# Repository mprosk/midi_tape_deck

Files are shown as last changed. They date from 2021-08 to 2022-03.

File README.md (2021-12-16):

# MIDI Tape Deck
MIDI controlled tape deck. Dynamically adjust the pitch of a recording to a specific pitch based on MIDI note data.

This project is built around the Yamaha KX-130 but can likely be adapted to other decks and mechanisms

## Theory of Operation

Cassette tapes are designed to run at a nominal rate of 1.75 inches per second. When the speed of tape playback is changed, the resulting sound will have a change in pitch. The slower the speed, the lower the pitch, and vice versa. By adjusting the speed of tape playback by a specific amount, the pitch of the recording can be changed to a specific note, assuming the nominal pitch of the recording is known.

This project provides the hardware and software for performing such a task.

### Speed Control

In the tape deck used in this project, the tape speed could be adjusted using a 1k potentiometer. The pitch range of the 1k pot was quite limited, meaning that few notes could be reached. Experimentation revealed that the larger the value of the potentiometer, the larger the change in frequency, and thus the more notes that could be tuned to. In addition, the change in pitch as a function of the change of resistance was observed to be linear.

Digital potentiometers are one way of interfacing digital and analog systems. The value of the pot can be changed in software but wired to the tape deck in place of the existing 1k pot. However, digital potentiometers typically have only 128 or 256 "taps" on them, meaning they can only stop at a fairly low number of values between the minimum and maximum values. This is in contrast to the mechanically actuated potentiometer, which can be adjusted continuously along is range.

Due to the low number of taps, a single digital potentiometer would not be able to control the tape deck with enough precision to reach a specific note. In order to mitigate this, two digital potentiometers were ganged together in the circuit shown below.

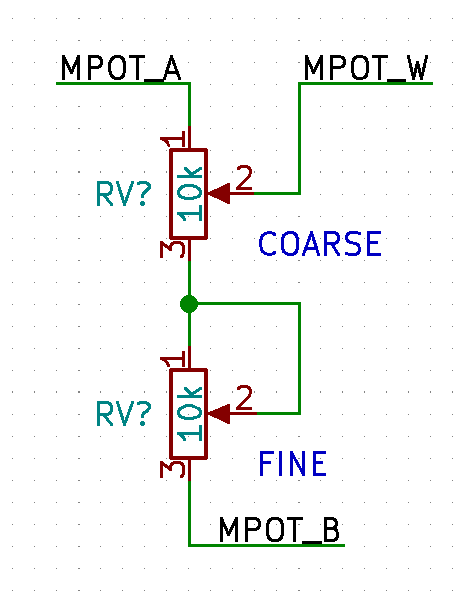
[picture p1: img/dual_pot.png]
dual_pot


This configuration results in one of the potentiometers causing a larger change in the overall resistance, while the other produced a larger change, creating a "coarse" setting and a "fine" setting. This configuration allowed for a much larger number of frequencies to be reached, as  instead of 256 discrete points, there were now 256<sup>2</sup> different combinations across the two potentiometers. 

### Transfer Function

The purpose of the potentiometers is to adjust the playback speed of the tape such that the frequency is changed by a target amount. In order to know what values to set the potentiometers to, we must know what the relationship between the potentiometer settings and the change in frequency is in the first place. By understanding this relationship, we can figure out what pot settings we need to obtain the desired change in pitch.

This system has two independent variables--the settings of the coarse and fine potentiometers--and one dependent variable--the change in pitch of the tape. By stepping through a range of combinations of potentiometers settings and recording the resulting pitch shift, we can start to see the relationship develop.

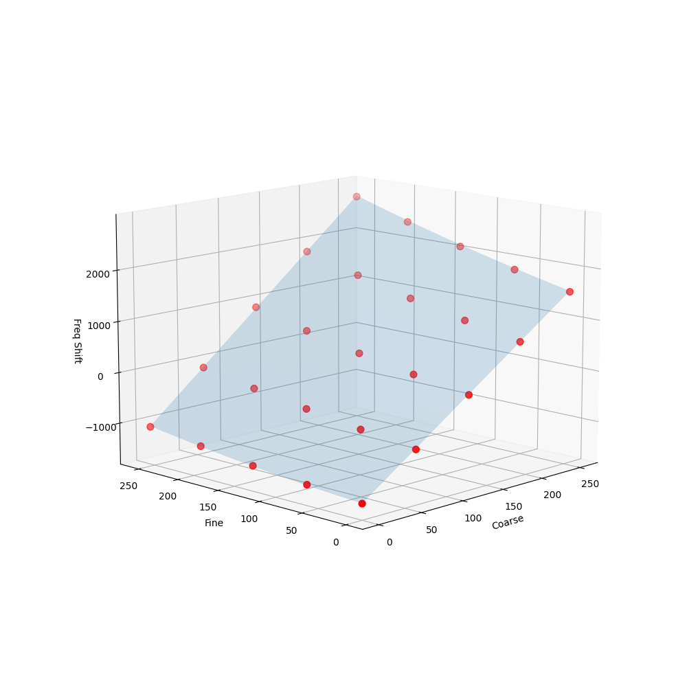
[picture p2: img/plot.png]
plot


Note that this relationship is only linear when the coarse potentiometer is changed, and is nonlinear when the fine potentiometer is changed. Also note how the coarse potentiometer has a greater impact on the output frequency than the fine potentiometer. 

Once we have captured enough data points, a best fit equation can be calculated for the surface using polynomial regression. This is performed in `eval/eval.py`. This produces a formula that equates the change in output frequency based on the coarse (x) and fine (y) potentiometer settings.

```
freq(x,y) = -1503.0871471 + 12.0767089x + 0.9015391y + 0.0115233xy + 0.003259y^2
```

### Equation Solver

Now that we are able to calculated the change in output frequency for a given combination of coarse and fine settings, we can start to work on the inverse: finding the combination of potentiometer settings that result in the desired change in output frequency.

Solving the equation mathematically for a given frequency is not conducive to an embedded device (or me) so this approach will be a little more brute-force, essentially a recursive guess-and-check.

First, the setting of the fine potentiometer is fixed to 127. A binary search is performed on the setting of the coarse potentiometer, using the equation above to determine what the output frequency will be. Once a coarse settings is found that puts the output close enough to the target value, the same operation is repeated for the fine potentiometer. Essentially the coarse pot is adjust to get the output close, then final adjustment is made using the fine pot.

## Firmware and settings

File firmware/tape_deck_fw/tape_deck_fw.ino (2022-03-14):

/***********************************************************************
 *  MIDI Tape Deck
 *
 *  DESCRIPTION
 *      <TODO>
 *
 *  REFERENCES
 *      
 * 
 ***********************************************************************/

/*=====================================================================*
    Local Header Files
 *=====================================================================*/


/*=====================================================================*
    Interface Header Files
 *=====================================================================*/
#include "mcp41hvx1.h"
#include "midi.h"
#include "notes.h"


/*=====================================================================*
    System-wide Header Files
 *=====================================================================*/
#include <Arduino.h>
#include <math.h>


/*=====================================================================*
    Pin Defines
 *=====================================================================*/
#define PIN_MODE_SW                 (2)
#define PIN_INT_1                   (3)
#define PIN_POT_COARSE              (A4)
#define PIN_POT_FINE                (A5)
#define PIN_LED                     (A0)


/*=====================================================================*
    Private Defines
 *=====================================================================*/
// #define DEBUG_PRINTOUT              /* Enables debug printing */
#define LED_BLINK_INTERVAL_MS       (1000u)

/*=====================================================================*
    Private Data Types
 *=====================================================================*/
/* None */


/*=====================================================================*
    Private Data
 *=====================================================================*/



/*=====================================================================*
    Ardunio Function Implementations
 *=====================================================================*/

void setup()
{

    // Initialize UART for MIDI
      Serial.begin(31250);      // This is the CORRECT MIDI baud rate
//    Serial.begin(32190);        // This is to compensate for the Virus's overzealous clock rate

    // Initialize GPIO
    pinMode(PIN_MODE_SW, INPUT_PULLUP);
    pinMode(PIN_LED, OUTPUT);
    digitalWrite(PIN_LED, LOW);
    

    // Initialize MCP41HVx1
    pinMode(PIN_POT_COARSE, OUTPUT);
    pinMode(PIN_POT_FINE, OUTPUT);
    digitalWrite(PIN_POT_COARSE, HIGH);
    digitalWrite(PIN_POT_FINE, HIGH);
    SPI.begin();
    SPI.beginTransaction(SPISettings(MCP41HVX1_SPI_CLK_HZ, MSBFIRST, SPI_MODE0));
}

/*---------------------------------------------------------------------*/

void loop()
{   
    uint8_t nominal = 0xFF;
    midi_note_t note;
    uint8_t mode_last = digitalRead(PIN_MODE_SW);
    digitalWrite(PIN_LED, mode_last);

    while(1)
    {
        // Check if we've changed control modes
        uint8_t mode = digitalRead(PIN_MODE_SW);
        if (mode != mode_last)
        {
            nominal = 0xFF;
            repitch(60, 60);
            digitalWrite(PIN_LED, mode);
        }
        mode_last = mode;

        // Process incoming MIDI notes
        midi_note_event_t note_event = midi_read(&note);
        if ((note_event == EVENT_NOTE_ON) && mode)
        {
            digitalWrite(PIN_LED, HIGH);

            // If the nominal pitch has not been set, record it now
            if (nominal == 0xFF) {
                nominal = note.note;
            }
            
            // Apply the repitching
            repitch(nominal, note.note);

#ifndef DEBUG_PRINTOUT
            // Delay breifly so the LED is more visible
            delayMicroseconds(1500);
#endif
            digitalWrite(PIN_LED, LOW);
        }
    }
}


/*=====================================================================*
    Private Function Implementations
 *=====================================================================*/

/*---------------------------------------------------------------------*
 *  NAME
 *      print_status
 *
 *  DESCRIPTION
 *      prints the current potentiometer settings
 *---------------------------------------------------------------------*/
void print_status(void)
{
#ifdef DEBUG_PRINTOUT
    Serial.print("Coarse: ");
    Serial.print(mcp41hvx1_get(PIN_POT_COARSE));
    Serial.print(" Fine: ");
    Serial.print(mcp41hvx1_get(PIN_POT_FINE));
    Serial.println();
#endif
}

/*---------------------------------------------------------------------*
 *  NAME
 *      repitch
 *
 *  DESCRIPTION
 *      sets the potentiometers to produce a target output
 *      note given the nominal note of the sample
 *---------------------------------------------------------------------*/
uint8_t repitch(uint8_t nominal, uint8_t target)
{
    float target_freq = get_note_freq(target);
    float target_percent = target_freq / get_note_freq(nominal);
    uint8_t x = single(target_percent);
    mcp41hvx1_set(PIN_POT_COARSE, x);

#ifdef DEBUG_PRINTOUT
    Serial.print("Target: "); Serial.print(target);
    Serial.print(" ("); Serial.print(target_freq); Serial.println(" Hz)");
    Serial.print("%% change: "); Serial.println(target_percent);
    print_status();
#endif
}


/*---------------------------------------------------------------------*
 *  NAME
 *      single
 *
 *  DESCRIPTION
 *      calculates the potentiometer setting needed to acheive
 *      the given percent change in frequency
 *---------------------------------------------------------------------*/
uint8_t single(float z)
{
    /* Equation for single 10k pot */
    float c = ceil(124.42 * z - 61.046);
    /* Equation for single 5k pot */
    // float c = ceil(196.08 * z - 132.02);
    if (c < 0)
    {
        return 0;
    }
    if (c > MCP41HVX1_TAP_COUNT - 1)
    {
        return MCP41HVX1_TAP_COUNT - 1;
    }
    return (uint8_t)round(c);
}

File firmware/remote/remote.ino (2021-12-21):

/***********************************************************************
 *  Dual Digipot Remote Control
 *
 *  DESCRIPTION
 *      Basic sketch for remotely operating the two digi pots over serial
 *
 *  REFERENCES
 *      MCP41HVx1 Datasheet - Microchip Technology Inc.
 * 
 ***********************************************************************/


/*=====================================================================*
    Interface Header Files
 *=====================================================================*/
#include "mcp41hvx1.h"


/*=====================================================================*
    Pin Defines
 *=====================================================================*/
#define PIN_POT_COARSE              (A4)
#define PIN_POT_FINE                (A5)


/*=====================================================================*
    Ardunio Function Implementations
 *=====================================================================*/

void setup()
{
    // Initialize UART
    Serial.begin(115200);
    Serial.setTimeout(15000);

    // Initialize MCP41HVx1
    pinMode(PIN_POT_COARSE, OUTPUT);
    pinMode(PIN_POT_FINE, OUTPUT);
    digitalWrite(PIN_POT_COARSE, HIGH);
    digitalWrite(PIN_POT_FINE, HIGH);
    SPI.begin();
    SPI.beginTransaction(SPISettings(MCP41HVX1_SPI_CLK_HZ, MSBFIRST, SPI_MODE0));
}

/*---------------------------------------------------------------------*/

void loop()
{
    long int val = 0;
    if (Serial.available())
    {
        switch (Serial.read())
        {
            case 'c':
                val = Serial.parseInt();
                if ((val >= 0) && (val < MCP41HVX1_TAP_COUNT))
                {
                    mcp41hvx1_set(PIN_POT_COARSE, (uint8_t)val);
                    print_status();
                }
                break;
                
            case 'f':
                val = Serial.parseInt();
                Serial.println(val);
                if ((val >= 0) && (val < MCP41HVX1_TAP_COUNT))
                {
                    mcp41hvx1_set(PIN_POT_FINE, (uint8_t)val);
                    print_status();
                }
                break;
                
            case 's':
                print_status();
                break;

            case 'z':
                mcp41hvx1_decrement(PIN_POT_COARSE);
                print_status();
                break;

            case 'x':
                mcp41hvx1_increment(PIN_POT_COARSE);
                print_status();
                break;

            case ',':
                mcp41hvx1_decrement(PIN_POT_FINE);
                print_status();
                break;

            case '.':
                mcp41hvx1_increment(PIN_POT_FINE);
                print_status();
                break;
                
            default:
                break;
        }
    }
}


/*=====================================================================*
    Private Function Implementations
 *=====================================================================*/

/*---------------------------------------------------------------------*
 *  NAME
 *      print_status
 *
 *  DESCRIPTION
 *      prints the current potentiometer settings
 *---------------------------------------------------------------------*/
void print_status(void)
{
    Serial.print("(");
    Serial.print(mcp41hvx1_get(PIN_POT_COARSE));
    Serial.print(",");
    Serial.print(mcp41hvx1_get(PIN_POT_FINE));
    Serial.println(")");
}

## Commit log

2021-08-02 Initial sketch
    [tape_deck_circuit.kicad_pcb, tape_deck_circuit.sch]
2021-08-02 Continue sketching out
    [tape_deck_circuit.sch]
2021-08-02 Complete basic schematic
    [tape_deck_circuit.sch]
2021-08-05 Fix SHDN signal on digipot
    [tape_deck_circuit.sch]
2021-08-05 Rename folders. Add test script firmware
    [tape_deck_circuit.kicad_pcb, tape_deck_circuit.sch]
2021-08-05 Allow chip select pin to be set dynamically. Don't use #def in module header
2021-08-10 add results of frequency response test
    [freq.xlsx]
2021-08-11 prototype remap code
    [freq.xlsx]
2021-08-16 Continue eval of frequency response
    [freq.xlsx, notes.xlsx]
2021-08-24 Add results from experiments with 2 digital pots
    [freq.xlsx, tape_deck_circuit.sch]
2021-08-27 Continue analyzing characteristic curves
    [freq.xlsx]
2021-08-30 Start working out protoboard layout
    [freq.xlsx, tape_deck_circuit.kicad_pcb, tape_deck_circuit.sch]
2021-08-31 mess with excel some more
    [freq.xlsx]
2021-08-31 Continue protoboard layout
    [tape_deck_circuit.kicad_pcb, tape_deck_circuit.sch]
2021-09-02 Add script for generating 3d plot of frequency curve
    [freq.xlsx]
2021-09-03 Try to solve for the equation
    [freq.xlsx]
2021-09-05 Get regression working. Start to sketch solver
    [dump.csv, dump_2d.csv, freq.csv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]
2021-09-05 Improve notes LUT
    [notes.xlsx]
2021-09-05 Clean up function prototypes
2021-09-16 Fix function misnaming in solve.py
    [solve.py]
2021-12-16 Add script for getting frequency measurements from SCPI device
2021-12-16 Take new measurements for 5k-5k pots and update values
    [5k-5k.csv, freq.xlsx]
2021-12-21 Capture data with new frequency change method. Archive old captures
    [10k-10k.csv, 5k-5k.csv, 5k-5kP1k5-3kHz.csv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]
2022-03-14 Get repitch working with only one 10k pot
    [10k-Single.xlsx, freq.xlsx, tape_deck_circuit.kicad_sch]
2022-03-14 Add the ability to set the nominal pitch value
2022-03-16 Clean up schematic
    [tape_deck_circuit.kicad_sch, tape_deck_circuit.sch]
2022-03-16 More cleanup of schematic files
2022-03-16 Start sketching out synth voice PCB
    [pitch_ctrl.kicad_sch, tape_deck_synth.kicad_pcb, tape_deck_synth.kicad_sch]
